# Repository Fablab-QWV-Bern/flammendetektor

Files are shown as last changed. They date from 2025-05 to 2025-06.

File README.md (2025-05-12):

# Flammendetektor der QWV

(ein Feuer-Alarm-System für den Lasercutter basierend auf einem UV-Sensor)

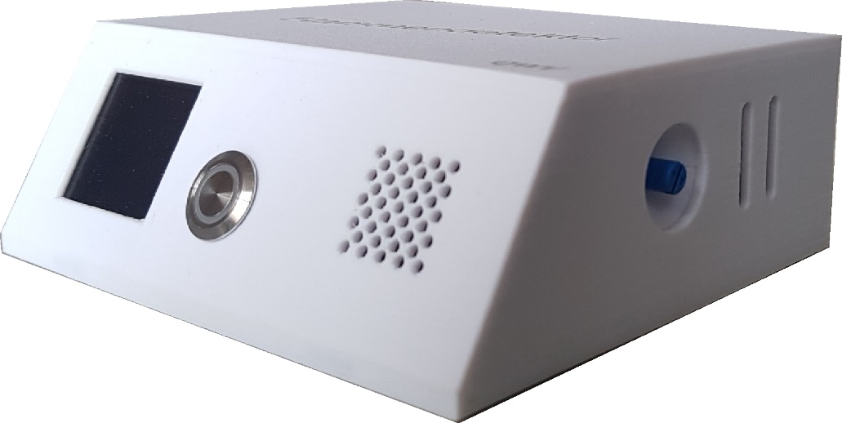
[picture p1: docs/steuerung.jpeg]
steuerung

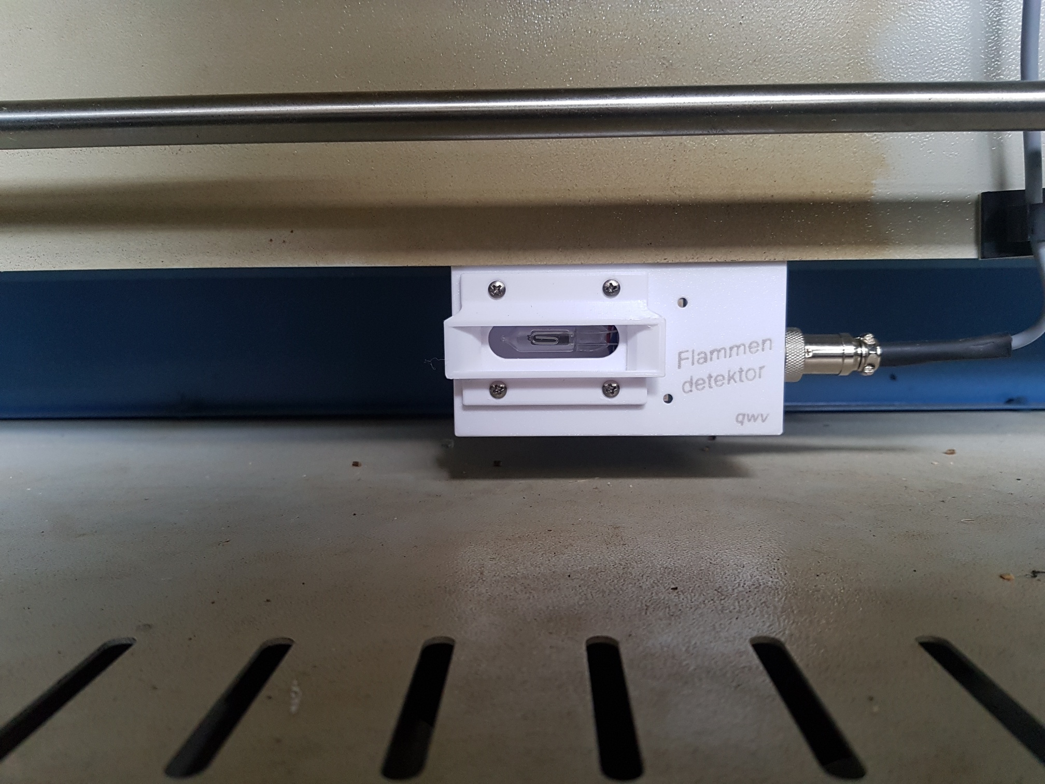
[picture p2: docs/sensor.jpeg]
sensor


## Warum?

Beim Gravieren oder Schneiden mit dem Laserstrahl entstehen immer wieder Flammen, die – wenn sie nicht sofort gelöscht werden – Schaden am Laserkopf oder sogar einen Brand verursachen können. 

Wann entstehen Flammen:

- kleinere Flammen am Laserpunkt und leichter Geruch können manchmal auftreten. 
- wenn die Druckluft bei der Linse am Laserkopf nicht eingeschaltet ist.
- wenn bei leicht entzündlichen Materialien eine zu hohe Leistung oder eine zu langsame Schnittgeschwindigkeit gewählt wird, oder sich starke Kunststoffablagerungen von früheren Arbeiten auf dem Gittertisch oder den dünnen Tragstäben aufgebaut haben.

Wie lösche ich Flammen:

- Zum Pausieren «▶ ∥» drücken 
- Wenn nötig Abdeckung öffnen und Flamme ausblasen 
- Sicherstellen, dass die Absaugung angeschaltet ist und das Manometer für die Druckluft bei der Linse ca. 3 bar anzeigt. 

(Bei manchem Material lässt es sich nicht vermeiden und dann ist es auch nicht weiter schlimm, wenn nur kleine Flammen entstehen). 

## Im Ernstfall

Bei größeren Flammen oder starker Rauchentwicklung muss das Lasern sofort unterbrochen werden, da sonst die Linse beschädigt wird:

- Deckel leicht öffnen (Laser wird ausgeschaltet, der Antrieb fährt jedoch weiter). 
- Laserprozess stoppen und den Laserkopf mit den Pfeil-Tasten am Bedienpult in eine von den Flammen entfernte Position fahren. 
- Deckel öffnen und versuchen die Flammen mit pusten oder abdecken zu löschen.
- Letzter Ausweg ist das Löschen mit dem CO2 -Löscher in kurzen Sprüh-stössen. Der passende Feuerlöscher befindet sich links beim Durchgang zum Metall-Raum an der Wand.
- **Bei weiterer Eskalation die Feuerwehr rufen**, anwesende Personen warnen und mit allen den Raum verlassen — Erstickungsgefahr durch CO2 und durch Rauch!

Bei einer permanenten Überwachung des Laservorgangs, kann der User sofort eingreifen. Dies genügt in der Regel, um Schaden zu vermeiden. 

Ruht aber der Blick nicht immer auf dem Laserprozess, dauert es oft zu lange, bis die Flammenbildung erkannt wird und es kommt zum Ernstfall.

> Der installierte Feuerdetektor kann den User nicht von der Überwachungspflicht befreien, ihm aber helfen rechtzeitig zu reagieren und grösseren Schaden zu vermeiden.

## **Funktion**

### Der **UV-Flammensensor**

überwacht den ganzen Arbeitsbereich auf vorhandene Flammen. Bei jeder erkannten Flamme, sendet der Sensor – gleichzeitig mit dem Blinken der gelben LED - Impulse an die Steuerung (je grösser die Flamme, umso höher ist die Puls-Frequenz).

### Steuerung

Bei jedem Impuls des Sensors erfolgt ein optisches (rote LED) und akustisches Signal am Bedienpult. Die Steuerung misst die Zeitspanne zwischen den letzten Impulsen (Frequenz) und bewertet so die Gefahrenstufe.
 Handelt es sich nur um ein kurzes oder kleines Aufflammen, so wird dies vorerst toleriert und keine Aktion ausgelöst. 

Sobald aber dauernd grössere Flammen erfasst werden, erscheint auf dem Display eine Gefahrenwarnung, begleitet von einem optischen (rote LED) und akustischen Alarm. 

Unternimmt der User nach drei Gefahrenmeldungen keine Massnahmen zur Verhinderung der Flammenbildung, so wird der Laservorgang unterbrochen. 
 Dies, mit der gleichen Wirkung, wie wenn die Pausen-Taste «▶ ∥» am Laser-Panel gedrückt worden wäre. 

➔ Der Laserkopf bleibt in seiner Position stehen und kann, nach dem Löschen der Flammen, den Laser-Auftrag weiterführen.

Dazu ist am Display die Reset-Taste und am Lasercutter-Panel die «ENTER»-Taste zu drücken.

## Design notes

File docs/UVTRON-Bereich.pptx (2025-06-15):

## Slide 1

hochempfindlicher UV-Sensor

UVTRON
R2868

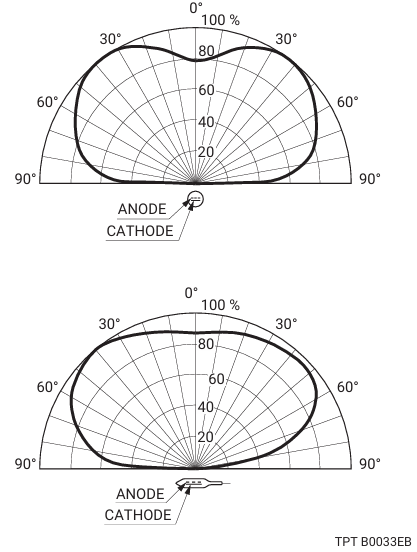
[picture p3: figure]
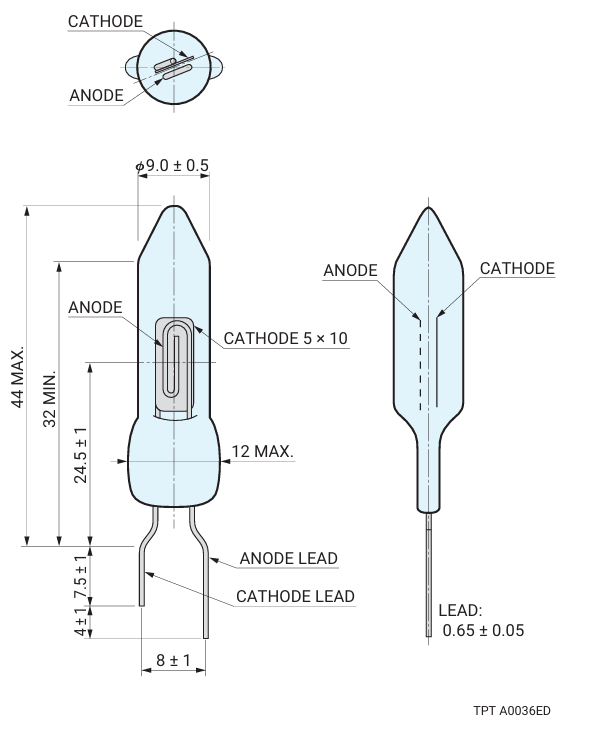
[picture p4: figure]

QWV-2024

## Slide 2

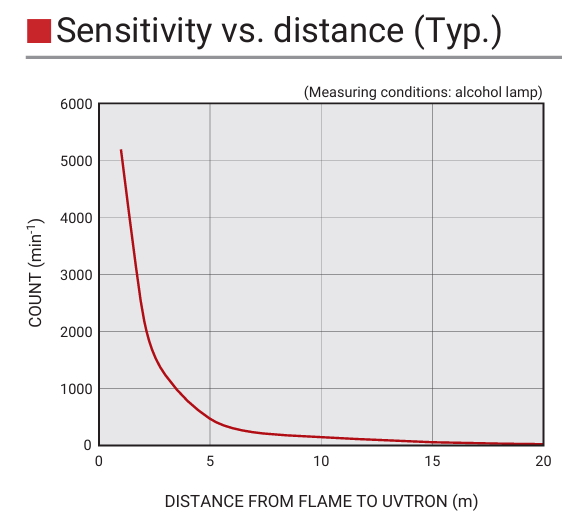
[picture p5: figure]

Einsatzbereich im Lasercutter 600 x 900 mm

1 m

QWV-2024

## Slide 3

Erkennungsbereich bei waagrechtem Einbau

QWV-2024

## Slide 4

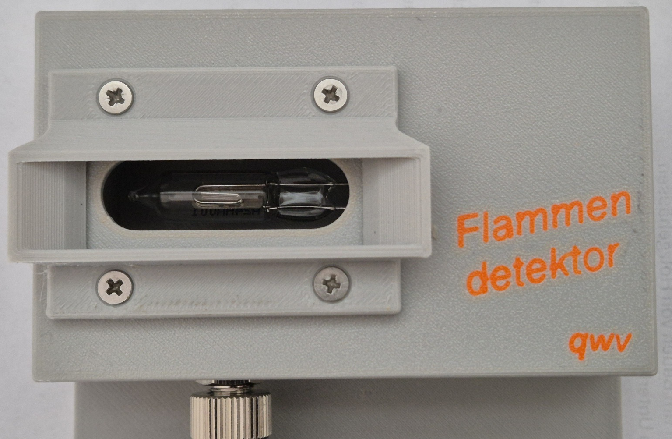
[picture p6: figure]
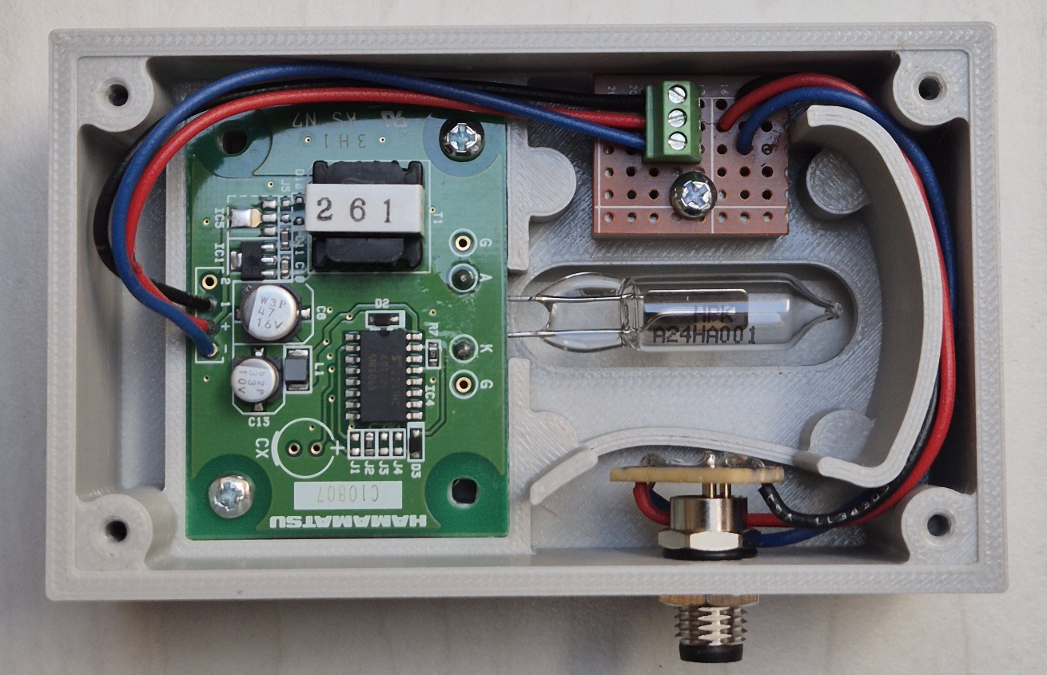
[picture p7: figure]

UV-Sensor R2868
von UVTRON

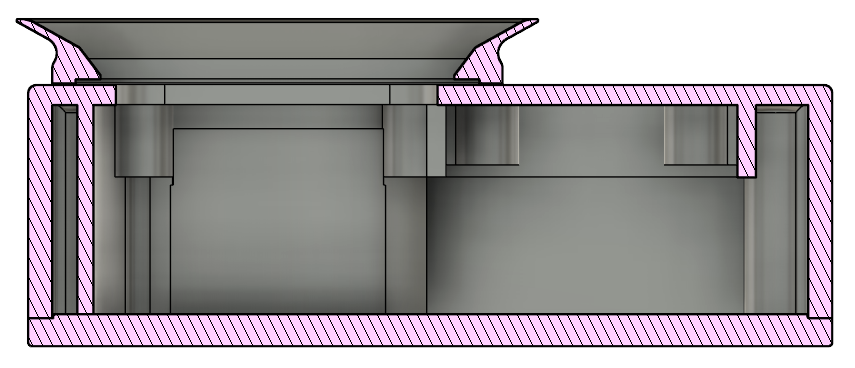
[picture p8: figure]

Steuerschaltung C10807
von UVTRON

QWV-2024

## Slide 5

Situation im Lasercutter AKJ 6090

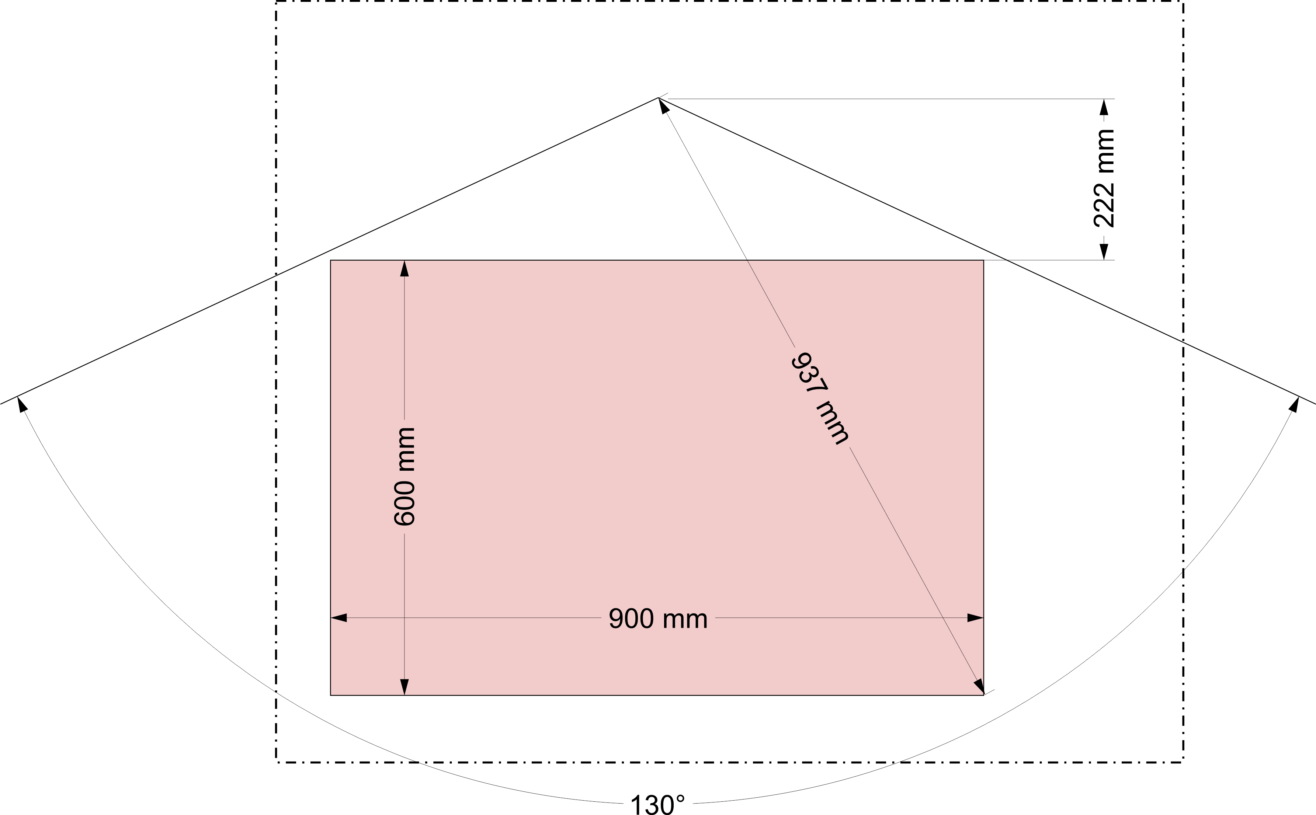
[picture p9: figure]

QWV-2024

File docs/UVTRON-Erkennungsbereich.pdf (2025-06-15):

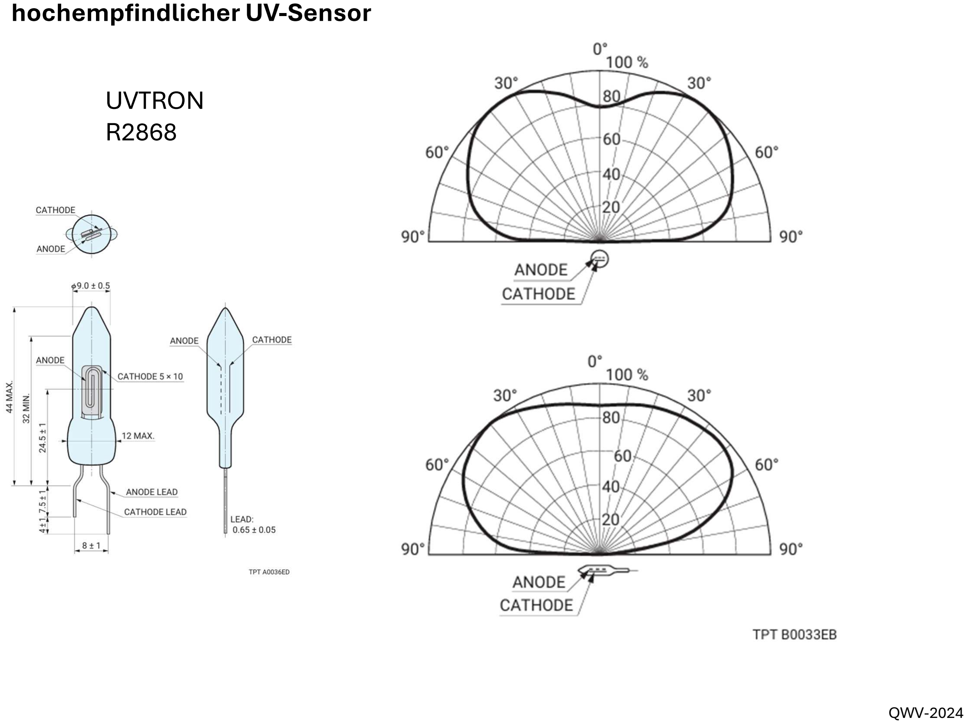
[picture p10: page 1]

UVTRON
R2868

QWV-2024

hochempfindlicher UV-Sensor

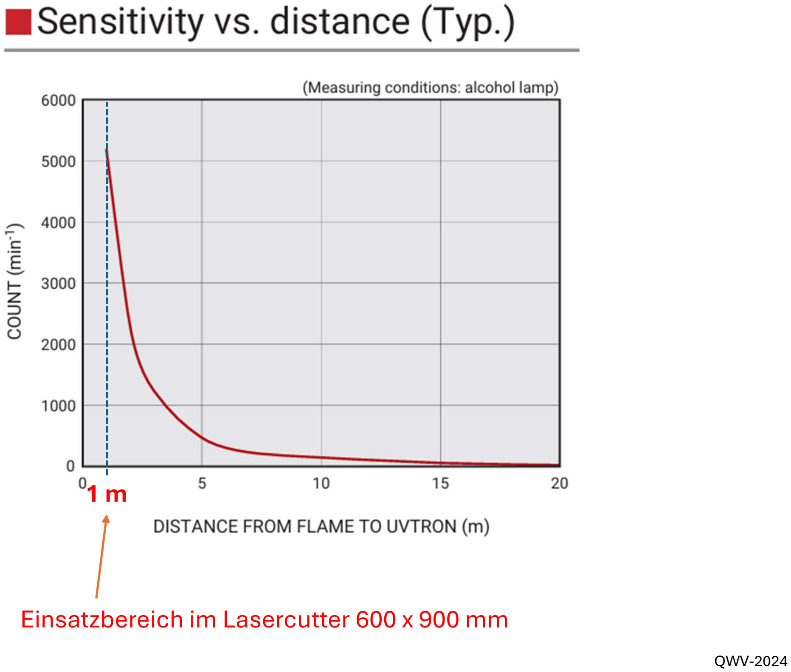
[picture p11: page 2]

### 1 m

Einsatzbereich im Lasercutter 600 x 900 mm

Erkennungsbereich bei waagrechtem Einbau

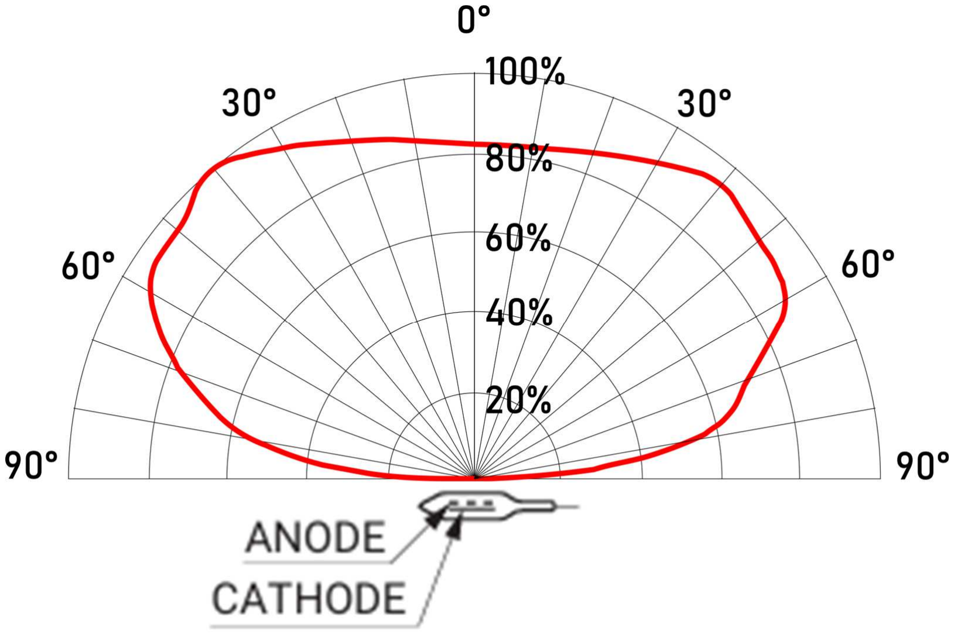
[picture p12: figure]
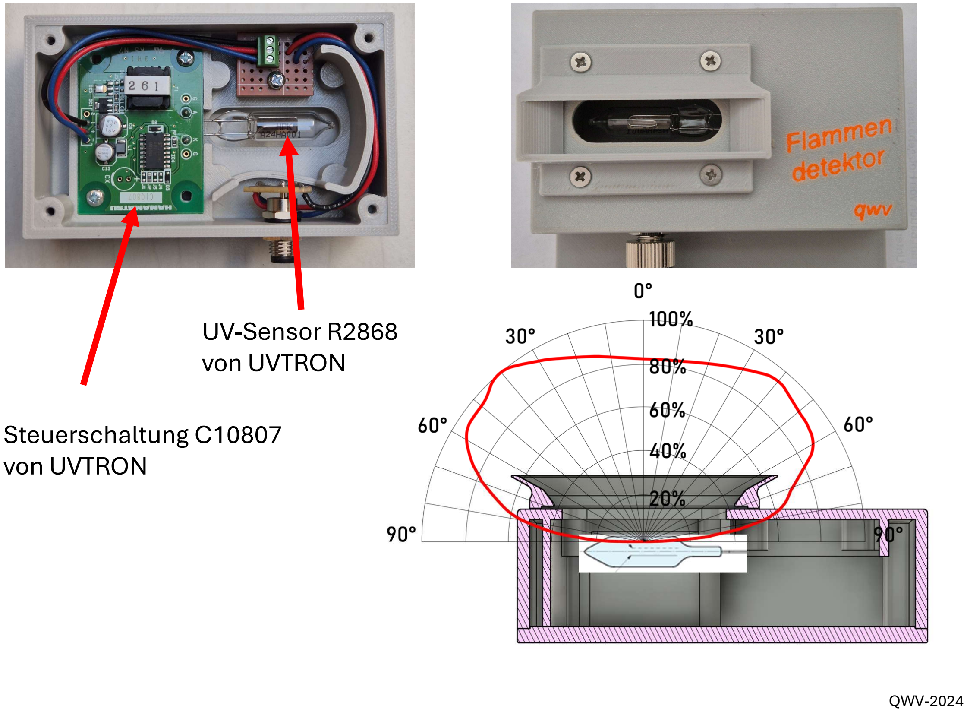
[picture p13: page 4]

Steuerschaltung C10807
von UVTRON

UV-Sensor R2868
von UVTRON

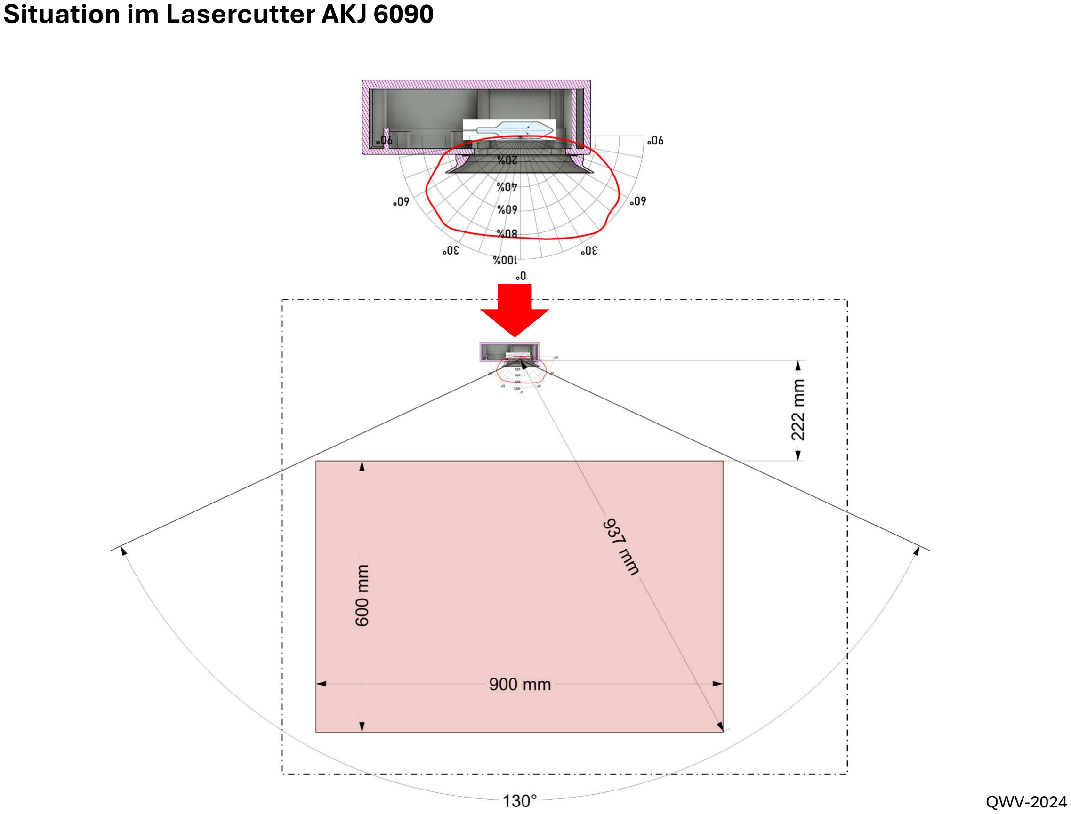
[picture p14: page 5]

Situation im Lasercutter AKJ 6090

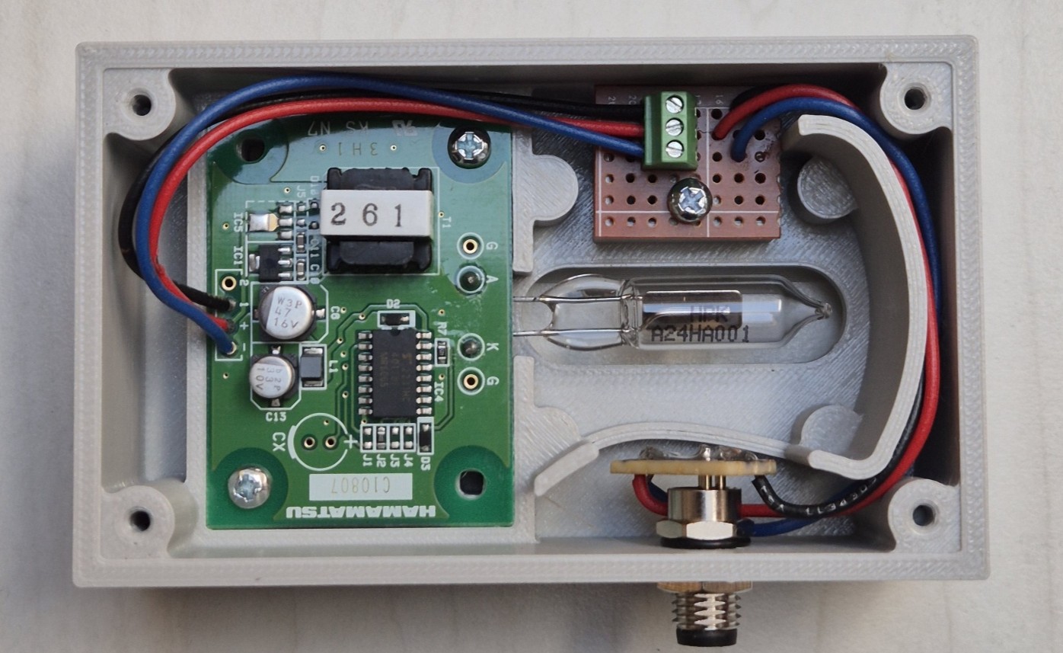
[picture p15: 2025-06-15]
docs/C10807-Gehaeuse-offen.jpg

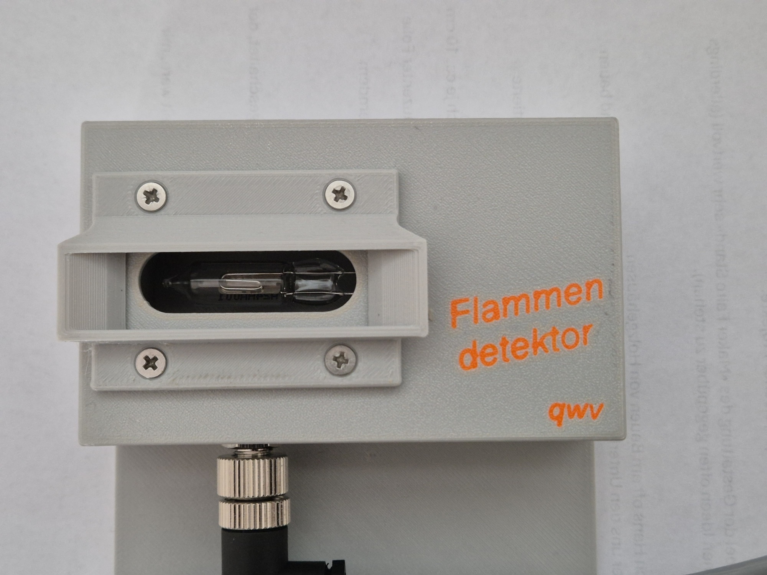
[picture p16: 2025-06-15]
docs/Sensorgehaeuse-vorne.jpg

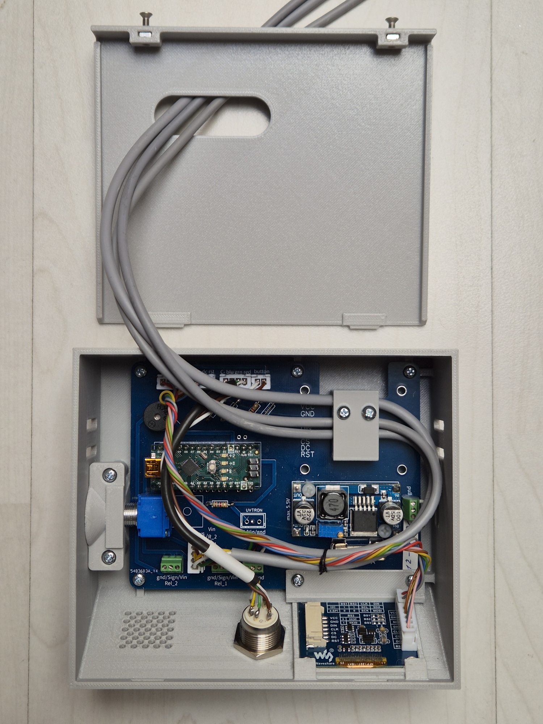
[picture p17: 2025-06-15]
docs/Flammendetektor-offen.jpg

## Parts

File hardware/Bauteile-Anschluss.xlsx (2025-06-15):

Flammen-Detektor Lasercutter QWV Baujahr 2025, 12-24 V Ausführung
Materialliste und Anschlussbelegung an Arduino Nano
Element |  | Bezeichnung | Pin | Bezugsquelle | Preis
Arduino Nano |  |  |  | Conrad (Art. Nr.1172623) | CHF 19.95
LM2596 Schaltregler DC-DC Step-Down (Abwärtswandler) Eingangsspannung: 3.2 – 40V Ausgangspannung: 1.25V – 35V (Einstellbar über Potentiometer) |  |  |  | bastelgarage.ch (Art. Nr.420103) | CHF 4.90
 | - |  | GND
 | 5.5 V | OUT über F 2 A | Vin
OLED Display 128x128 1.5“ weiss I2C SPI |  | DIN | D 11 | bastelgarage.ch (Art. Nr. 420595) | CHF 16.50
 |  | CLK | D 13
 |  | CS | D 10
 |  | DC | D 7
 |  | RST | D 8
 |  | VCC | 5 V
 |  | GND | GND
HAMAMATSU Treiber-Schaltung C10807 mit HAMAMATSU Flammensensor UVTRON R2868 |  | - | GND | AliExpress inkl. Transport | CHF 75.80
 |  | + | V in | Zoll-CH | CHF 18.00
 |  | 1 | D 3
Bourns 91A1A-B28-A15L 91A1A-B28-A15L Dreh-Potentiometer Mono 2 W 10 kΩ |  | 1 | 5 V | Conrad.ch (Bestell-Nr.:1055304) | CHF 5.65
 |  | mitte | A 0
 |  | 2 | GND
Piezo Buzzer Summer aktiv |  | - | GND | bastelgarage.ch (Art. Nr. 420248) | CHF 1.50
 |  | + | D 6
16mm Drucktaster mit RGB Beleuchtung 5V - Edelstahl (Vorwiderstand bereits integriert) | C | - | GND | bastelgarage.ch (Art. Nr. 420866) | CHF 19.90
 | LED_Rot | + | D 4
 | LED_Grün | + | D 5
 | LED_Blau | + | D1
 | Taster | 1 | GND
 | Taster | 2 | D 2
Gravity Digitales 5A Relais Modul | Relais 1 | - | GND | bastelgarage.ch (Art. Nr. 421668) | CHF 6.90
 | Relais 1 | + | V in
 | Relais 1 | D | D 9
Gravity Digitales 5A Relais Modul (Option) | Relais 2 | - | GND | bastelgarage.ch (Art. Nr. 421668)
 | Relais 2 | + | V in
 | Relais 2 | D | D 12
2 x Feinsicherung Halter Clip für Printmontage |  |  |  | bastelgarage.ch (Art. Nr.420670) | CHF 0.40
521020 Feinsicherung (Ø x L) 5 mm x 20 mm 2 A 250 V Mittelträge -mT |  |  |  | Conrad.ch (Bestell-Nr.:535834 - 62)
3 Pol. Female cable connector, angled RND 205-01158 |  |  |  | distrelec (Art. Nr.301-64-683) | CHF 14.80
3 Pol. Einbaustecker Sensor Circular Panel mount plug RND 205-01132 |  |  |  | distrelec (Art. Nr.301-64-657) | CHF 5.90
Drucksensor G1/4 1.2Mpa Analog (für Option, noch nicht eingebaut) | rot | + | V in | bastelgarage.ch (Art. Nr.422539)
 | schwarz | - | GND
 | gelb | Signal | A6
Div. Stiftleisten, Kabel und Stecker, Schrauben, kl. Bauteile |  |  |  | diverse | CHF 6.00
Leiterplatte |  |  |  | JLCPCB | CHF 0.00
 |  |  |  |  | CHF 196.20

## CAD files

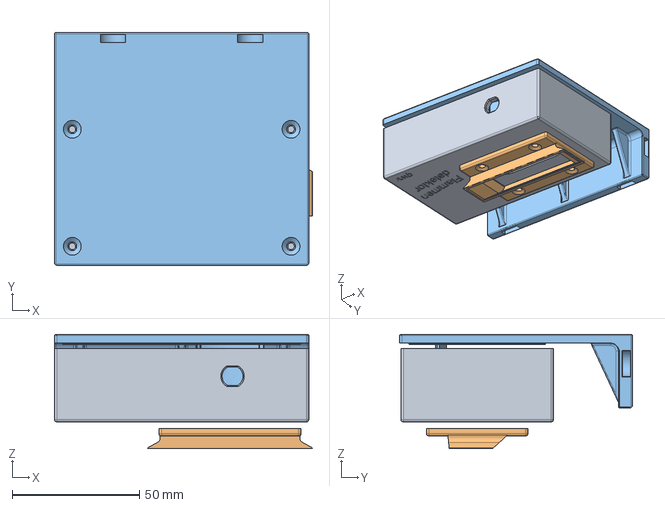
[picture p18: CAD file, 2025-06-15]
printables/UVTRON-Gehaeuse-Version-12Volt v8.step
101.4 x 91.5 x 45.0 mm

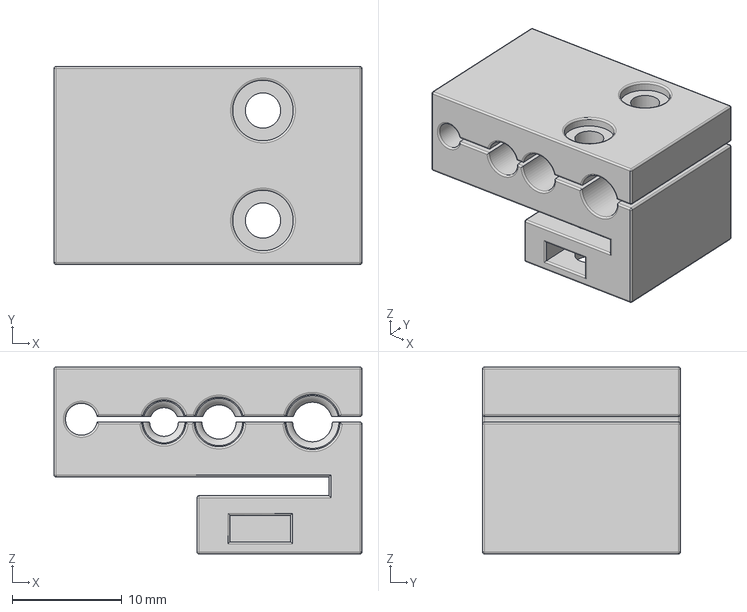
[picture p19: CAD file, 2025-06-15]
printables/Kabelhalter v5.step
28.0 x 18.0 x 17.0 mm

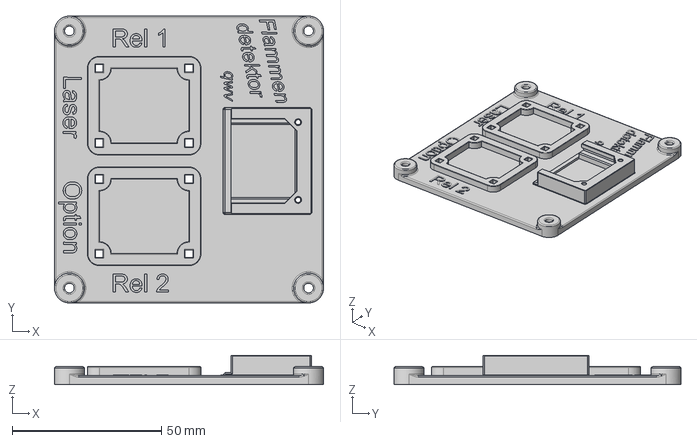
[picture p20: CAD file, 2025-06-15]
printables/Relaisträger v8.step
90.0 x 96.0 x 9.80 mm

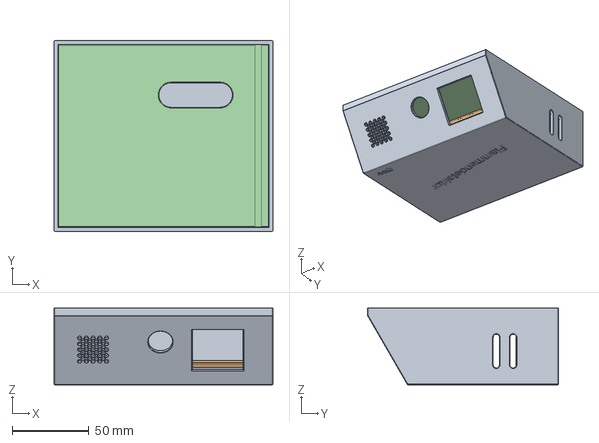
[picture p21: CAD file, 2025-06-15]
printables/Flammendetektor-Gehaeuse-2025.step
143.0 x 124.5 x 50.0 mm

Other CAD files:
printables/Flammendetektor-Gehaeuse-2025.stl
printables/Kabelhalter v5.stl
printables/Relaisträger v8.stl
printables/UVTRON-Gehaeuse-Version-12Volt v8.stl

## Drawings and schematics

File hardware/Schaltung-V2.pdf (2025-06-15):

# GND red grn

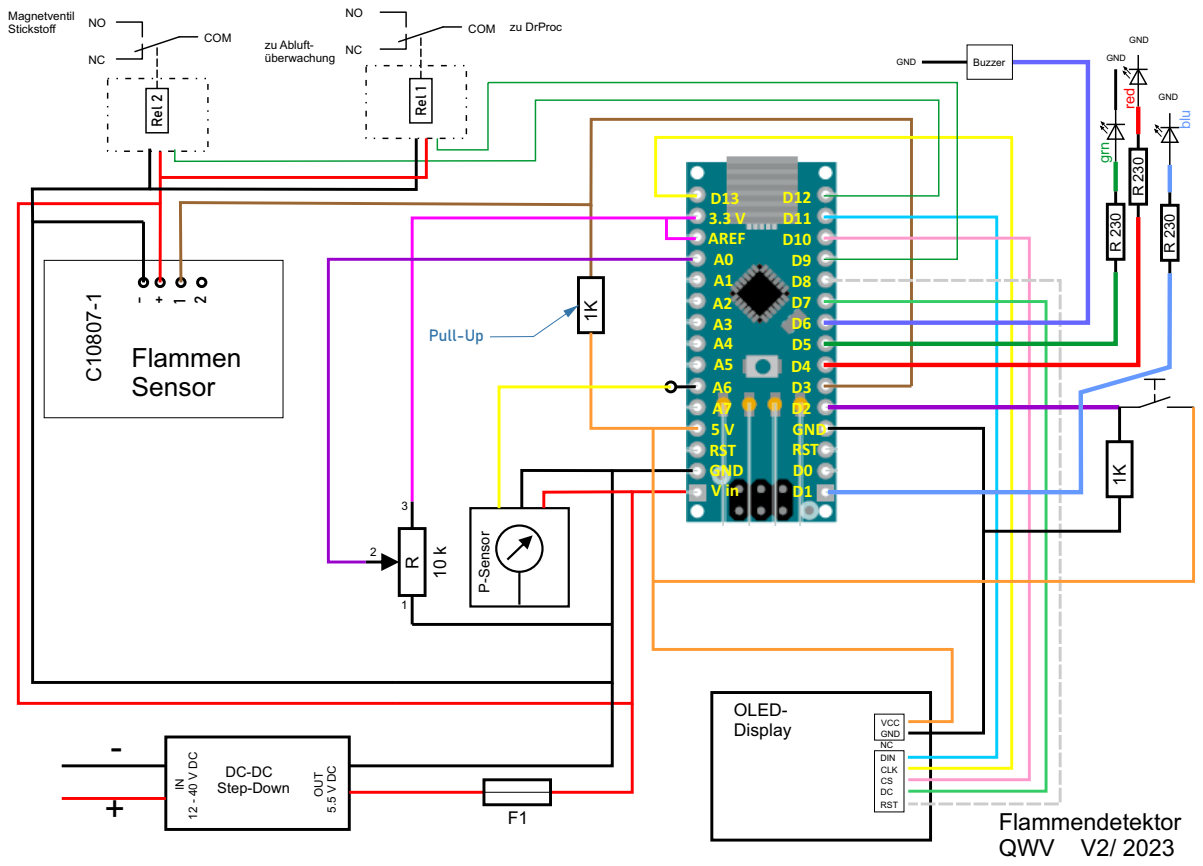
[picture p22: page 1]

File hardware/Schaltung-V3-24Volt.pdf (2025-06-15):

# GND red grn

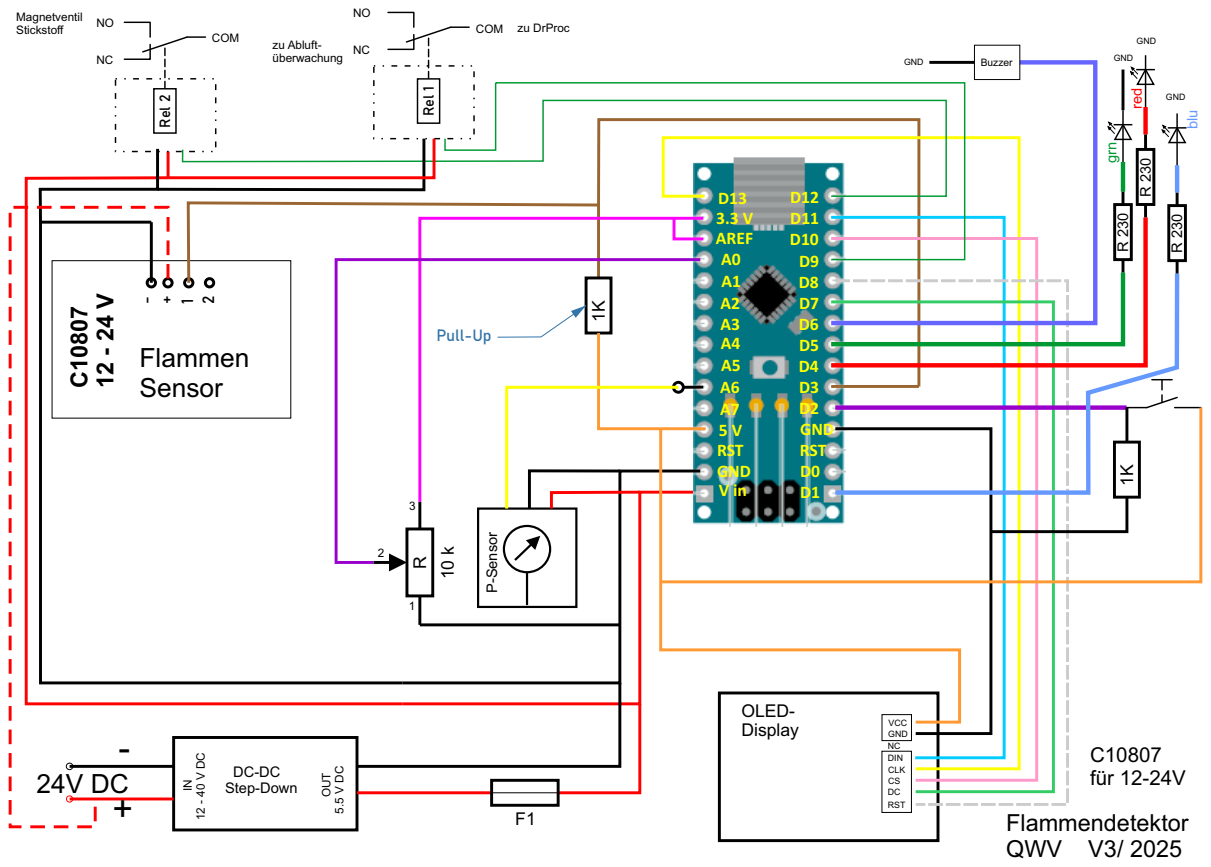
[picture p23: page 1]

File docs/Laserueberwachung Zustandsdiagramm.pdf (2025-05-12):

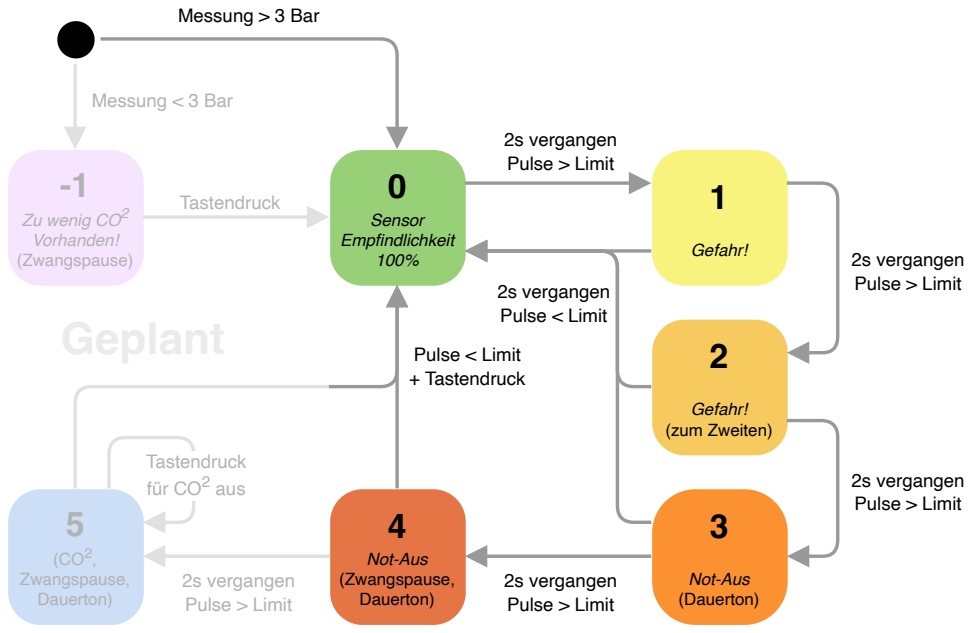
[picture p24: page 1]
Sensor Empfindlichkeit 100%; Messung > 3 Bar; Gefahr!; Not-Aus (Dauerton); Not-Aus (Zwangspause, Dauerton); 2s vergangen Pulse > Limit; 2s vergangen Pulse < Limit; Gefahr! (zum Zweiten); Pulse < Limit + Tastendruck; (CO²,; Zwangspause, Dauerton); Messung < 3 Bar; Tastendruck; Tastendruck für CO² aus

Zu wenig CO²
Vorhanden!
(Zwangspause)
Geplant

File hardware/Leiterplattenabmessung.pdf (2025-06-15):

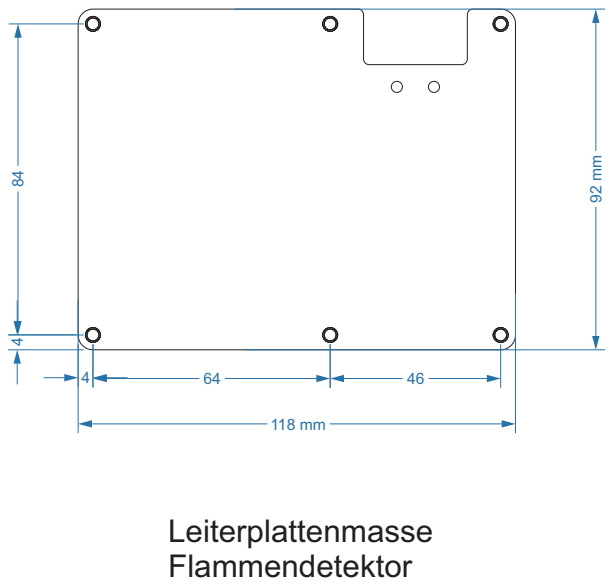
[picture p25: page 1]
Leiterplattenmasse Flammendetektor

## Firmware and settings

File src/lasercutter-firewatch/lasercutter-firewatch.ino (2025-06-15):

/*
  Flammendetektor für Lasercutter
  Platine C10807  12-24 Volt

  Peter Schurter
  Matthias Roggo 

  Quartierwerkstatt Vikoria Bern
*/

#include <Wire.h>
#include <Arduino.h>
#include <U8x8lib.h>
#ifdef U8X8_HAVE_HW_SPI
#include <SPI.h>
#endif

// Config
#define PULSE_LIMIT_HZ 1.0  // Pulsrate, über welcher eine Warnung ausgelöst wird

// Pins
#define LED_R 4
#define LED_G 5
#define LED_B 1
#define BUZZER 6  // Piezo-Lautsprecher
#define BUTTON 2
#define PAUSE_LASER 12  // Relais zur Pausierung des Lasers
#define AIR_EXTINGUISH 9  // Relais zur Druckluftsteuerung
#define SENSOR 3
#define POT_INPUT PIN_A0

enum LedColor {
  OFF = 0B000,
  GREEN = 0B010,
  RED = 0B100,
  BLUE = 0B001,
  PINK = 0B101
};

volatile boolean display_needs_full_redraw = true;

// Any timestamps will overflow after 49 days. This is much longer than the
// expected operation time of the laser and can be ignored.
volatile unsigned long pulse_dt_ms = ULONG_MAX;
volatile bool pulse_update = false; // flag to notifiy about new pulses (and trigger frequency estimation)

// Display driver parameters:          CLK data CS  DC RST
U8X8_SSD1327_WS_128X128_4W_SW_SPI u8x8(13, 11,  10, 7, 8  );

void setup(void) {
  analogReference(EXTERNAL); // AREF connected to Nanos 3.3V

  pinMode(LED_R, OUTPUT);
  pinMode(LED_G, OUTPUT);
  pinMode(LED_B, OUTPUT);
  pinMode(BUZZER, OUTPUT);
  pinMode(SENSOR, INPUT);
  pinMode (PAUSE_LASER, OUTPUT);
  pinMode (AIR_EXTINGUISH, OUTPUT);

  digitalWrite(BUZZER, LOW);
  set_led(BLUE);

  Serial.begin(9600);
  u8x8.begin();

  u8x8.setFont(u8x8_font_px437wyse700b_2x2_f);
  u8x8.drawString(0, 1, "FLAMMEN");
  u8x8.drawString(0, 5, "Detektor");

  u8x8.setFont(u8x8_font_8x13_1x2_r);
  u8x8.drawString(3, 8, "Info im");
  u8x8.drawString(3, 10, "Handbuch");
  u8x8.drawString(3, 12, "beachten");

  delay(3000);

  attachInterrupt(digitalPinToInterrupt(BUTTON), handle_button, RISING);
  attachInterrupt(digitalPinToInterrupt(SENSOR), handle_pulse_flank, CHANGE);

  u8x8.clearDisplay() ;
  set_led(GREEN);
}

LedColor set_led(LedColor color) {
    static LedColor current = OFF;
    digitalWrite(LED_R, color & 0b100);
    digitalWrite(LED_G, color & 0b010);
    digitalWrite(LED_B, color & 0b001);
    LedColor previous = current;
    current = color;
    return previous;
};

void handle_pulse_flank() {
  if (digitalRead(SENSOR)) {
    handle_pulse_end();
  } else {
    handle_pulse_start();
  }
}

volatile unsigned long pulse_start_ms = 0;
void handle_pulse_start() {
  pulse_start_ms = millis();
}

volatile unsigned long pulse_previous_ms = 0;
void handle_pulse_end() {
  unsigned long now = millis();

  unsigned long pulse_width_ms = now - pulse_start_ms;
  if (pulse_width_ms < 7 || pulse_width_ms > 14) {
    // This was a glitch, not a proper pulse
    Serial.print("Glitch detected (");
    Serial.print(pulse_width_ms);
    Serial.println(" ms)");
    return;
  }
  Serial.print("Pulse detected with ");
  Serial.print(pulse_width_ms);
  Serial.println(" ms");

  pulse_dt_ms = now - pulse_previous_ms;
  pulse_previous_ms = now;

  if (pulse_previous_ms != 0) {
    pulse_update = true;
  }
}

volatile uint8_t warning_state = 0; // the state machines "state"
volatile boolean button_pressed = false; // flag to check for button presses
void loop(void) {
  static uint8_t sensitivity_percent_previous = -1; // to check if the display needs an update
  static double pulse_hz = 0;
  static unsigned long pause_state_transition = 0; // allows to pause within a state after entering it

  boolean display_pulse_hz_update = false;

  float pulse_hz_upper_bound = 1000.0/(millis() - pulse_previous_ms);

  // Handle detected pulse
  if (pulse_update) {
    pulse_update = false;

    Serial.print("Intervall: ");
    Serial.println(pulse_dt_ms);

    // Notify about pulse
    LedColor previous = set_led(PINK);
    digitalWrite(BUZZER, HIGH);
    delay(50);
    if (warning_state != 4) {
      // In state 4 (emergency stop), the buzzer runs continuously. 
      // We don't want to interfere with that!
      digitalWrite(BUZZER, LOW);
    }
    set_led(previous);

    // Update pulse rate estimation
    pulse_hz = 1000.0/pulse_dt_ms;
    display_pulse_hz_update = true;

  } else if (pulse_hz_upper_bound < pulse_hz) {
    // Update the pulse Hz estimation, as it can be guaranteed to be lower.
    // Reduce display update rate:
    if (round(pulse_hz*100) != round(pulse_hz_upper_bound*100)) {
      pulse_hz = pulse_hz_upper_bound;
      display_pulse_hz_update = true;
    }
  }

  uint32_t potVal = analogRead(POT_INPUT);

  uint8_t sensitivity_percent = map(potVal, 0, 1020, 50, 100);
  double effective_pulse_limit_hz = ((double) PULSE_LIMIT_HZ)/(sensitivity_percent)*100;

  if (warning_state == 0) {
    //--- Update within state: No warnings ---//

    if (display_needs_full_redraw) {
      u8x8.clearDisplay();
      u8x8.setFont(u8x8_font_px437wyse700b_2x2_f);
      u8x8.drawString(1, 2, " ");
      u8x8.drawString(1, 2, "Sensor-");
      u8x8.setFont(u8x8_font_8x13_1x2_r);
      u8x8.drawString(0, 5, " ");
      u8x8.drawString(0, 5, "EMPFINDLICHKEIT");
      u8x8.drawString(1, 10, "         ");
      u8x8.drawString(1, 8, "          ");
    }

    if (display_pulse_hz_update || display_needs_full_redraw) {
      u8x8.setFont(u8x8_font_8x13_1x2_r);
      u8x8.drawString(0, 12, "Pulse:       ");
      u8x8.setCursor(7, 12);
      u8x8.print(pulse_hz);
      u8x8.print(" Hz  ");
    }

    if (sensitivity_percent != sensitivity_percent_previous || display_needs_full_redraw) {
      u8x8.setFont(u8x8_font_8x13_1x2_r);
      u8x8.setCursor(6, 8);
      u8x8.print(sensitivity_percent);
      u8x8.print(" % ");

      u8x8.drawString(0, 14, "Limit:       ");
      u8x8.setCursor(7, 14);
      u8x8.print(effective_pulse_limit_hz);
      u8x8.print(" Hz  ");
      sensitivity_percent_previous = sensitivity_percent;
    }
    display_needs_full_redraw = false;
  }

  if (pause_state_transition > millis()) return;

  // Check for state transitions
  if (pulse_hz < effective_pulse_limit_hz && (warning_state != 4 || button_pressed)){
    // Pulse frequency is below limit.
    if (warning_state != 0) {
      warning_state = 0;
      display_needs_full_redraw = true;
      pause_state_transition = 0;

      //--- Entering state: No warnings ---//
      set_led(GREEN);
      digitalWrite(BUZZER, LOW);
      digitalWrite(PAUSE_LASER, LOW);
    }
    return;
  } 

  // Pulse frequency is above limit.
  // Move to next warning state (if not at highest)
  if (warning_state < 4) {
    warning_state++;
    display_needs_full_redraw = true;
  } else {
    // No state change, since we're already at the highest
    return;
  }

  if (warning_state == 1 || warning_state == 2) {
    //--- Entering state: Limit exceeded once or twice ---//
    u8x8.clearDisplay();
    set_led(RED);

    u8x8.setFont(u8x8_font_px437wyse700b_2x2_f);
    u8x8.drawString(1, 5, "GEFAHR!");
    u8x8.setCursor(6, 9);
    u8x8.print(warning_state);

    pause_state_transition = millis() + 2*1000;
  }

  if (warning_state == 3) {
    //--- Entering state: Announce emergency pause ---//
    digitalWrite(BUZZER, HIGH);
    set_led(RED);
    
    u8x8.clearDisplay();
    u8x8.setFont(u8x8_font_px437wyse700b_2x2_f);
    u8x8.drawString(2, 5, "START");
    u8x8.drawString(1, 8, "NOT-AUS");

    pause_state_transition = millis() + 2*1000;
  }

  if (warning_state == 4) {
    //--- Entering state: Emergency pause ---//
    button_pressed = false;
    digitalWrite(BUZZER, HIGH);
    set_led(RED);

    u8x8.clearDisplay();
    u8x8.setFont(u8x8_font_8x13_1x2_r);
    u8x8.drawString(0, 1, "Taster druecken!");
    u8x8.drawString(0, 4, "Wenn Feuer");
    u8x8.drawString(2, 6, "GELOESCHT!");
    u8x8.drawString(0, 9, "Fortfahren  mit");
    u8x8.drawString(3, 11, "* ENTER * ");
    u8x8.drawString(0, 13, "auf LASER-PANEL");

    digitalWrite(PAUSE_LASER, HIGH);
  }
}

void handle_button() {
  button_pressed = true;
}

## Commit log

2023-09-15 move to millis, show warning state
2025-06-15 C10807 12-24V, fixes
    [Bauteile-Anschluss.xlsx, Flammendetektor-Gehaeuse-2025.step, Flammendetektor-Gehaeuse-2025.stl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]
